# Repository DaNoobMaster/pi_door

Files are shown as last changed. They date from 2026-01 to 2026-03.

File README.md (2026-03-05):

#Pi_Door
This project is a smart door lock created using a raspberry pi zero 2w. This is the cheapest raspberry pi capable of running what i want this project needs.
The door is capable of Face ID, Palm vein recognition, fingerprint and has a 4x4 keypad entry as well. QR codes can be generated for one time use to open the door as well.
It uses high-end secure biometric components in order to keep it reliable and safe. There is a live camera feed as well that would be transmitted from the camera to the local raspberry pi server.

The aim of this project is to make entering my house quicker and more reliable. Due to the fact that its mostly digital, it is less susceptible to intruder attacks and can help catch intruders if an attack does occur. The live camera feed is also helpful in checking who is at your at door. I belive this project would use my skills to the most. Its mechanical and software aspect is perfect for me to improve my skills and learn how to work with such types of hardware.

The 4x3 keypad can be used to enter in a pincode.
The pincode can be set to be however long.
Pressing # enters the code while * resets it. If no user input is present for 10 seconds, the code entry cache resets. If the door unlocks using other means, the code entry cache resets.




### Complete Hardware Wiring

| Subsystem | Device Pin / Signal | Connected To | Raspberry Pi Pin | GPIO / Voltage | Notes |
|---|---|---|---|---|---|
| **AI Camera (Face / Palm)** | VCC | Pi 5V | Pin 4 | 5V | Camera power |
| AI Camera | GND | Pi GND | Pin 6 | GND | Common ground |
| AI Camera | UART_TX | Pi RX | Pin 10 | GPIO15 (RXD) | Camera → Pi |
| AI Camera | UART_RX | Pi TX | Pin 8 | GPIO14 (TXD) | Pi → Camera |
| **Fingerprint Sensor (via CP2102)** | VIN | CP2102 3V3 | — | 3.3V | Sensor power |
| Fingerprint | GND | CP2102 GND | — | GND | Common ground |
| Fingerprint | RX | CP2102 TXD | — | UART TX |
| Fingerprint | TX | CP2102 RXI | — | UART RX |
| Fingerprint | RST | CP2102 DTR | — | Reset |
| CP2102 | USB | Raspberry Pi | USB | — | USB-UART |
| **3×4 Keypad** | K1 (Row 1) | Pi GPIO | Pin 29 | GPIO5 | Output |
| Keypad | K2 (Row 2) | Pi GPIO | Pin 31 | GPIO6 | Output |
| Keypad | K3 (Row 3) | Pi GPIO | Pin 33 | GPIO13 | Output |
| Keypad | K4 (Row 4) | Pi GPIO | Pin 35 | GPIO19 | Output |
| Keypad | K5 (Col 1) | Pi GPIO | Pin 37 | GPIO26 | Input (PU) |
| Keypad | K6 (Col 2) | Pi GPIO | Pin 38 | GPIO20 | Input (PU) |
| Keypad | K7 (Col 3) | Pi GPIO | Pin 40 | GPIO21 | Input (PU) |
| Keypad | K8 | — | — | NC | Not connected |
| Keypad | K9 | — | — | NC | Not connected |
| Relay | Relay VCC | Pi 5V | Pin 4 | 5V | Coil power |
| Relay | Relay GND | Pi GND | Pin 6 | GND | Ground |
| **Transistor (BC107)** | Base | Pi GPIO (via resistor) | Pin 16 | GPIO23 | Drives relay |
| Transistor | Collector | 5V | — | 5V | From voltage convertor |
| Transistor | Emitter | Relay Coil | — | — | Reference |
| **Solenoid Lock** | + | External Supply | — | +7.5V | Lock power |
| Solenoid | − | Relay NO Contact | — | Switched | Controlled by relay |

### Authentication Accuracy & Error Rates

| Input Method | False Acceptance Rate (FAR) | False Rejection Rate (FRR) | Notes |
|---|---|---|---|
| Fingerprint (Capacitive) | ~0.001% – 0.01% | ~1% – 3% | High accuracy, may fail with wet or damaged fingers |
| Face Recognition (Offline AI) | ~0.1% – 1% | ~1% – 5% | Affected by lighting, pose, and occlusion |
| Palm Recognition (Offline AI) | ~0.01% – 0.1% | ~0.5% – 2% | Very stable, less affected by lighting |
| Keypad PIN (4-digit) | 0% (if secret) | User-dependent | Security depends on PIN secrecy and length |

BOM

| S.No | Component | Purpose | Estimated Cost (₹) |
|-----:|---|---|---:|
| 1 | Solenoid (Door Lock) | Physically locks/unlocks the door | 800 |
| 2 | Face ID & Palm Vein Sensor | Primary biometric authentication | 5636 |
| 3 | Fingerprint Sensor | Secondary authentication | 2,042.00 |
| 4 | Raspberry Pi Zero 2 W | Main controller & processing unit | 1,587.10 |
| 5 | 18650 Battery | Portable power source | 205.32 |
| 6 | Battery Charger Module | Charging the 18650 battery | 14.00 |
| 7 | Battery Holder | Secure battery mounting | 46.00 |
| 8 | UART Converter (CP2102) | Additional UART interface for fingerprint sensor | 300.00 |
| 9 | USB to Micro-USB Cable | Power & USB connection | 54.00 |
| 10 | Barrel Jack Connector | External power input | 23.00 |
| 11 | 4×3 Keypad | Manual PIN-based fallback access | 188.00 |
| 12 | BC107 Transistor | Solenoid driver / switching | 19.00 |
| 13 | 3D Printed Parts | Enclosure & mounting brackets | — |
| 14 | Acrylic Sheet | Structural housing panels | 75.00 |
| 15 | SRD-05VDC-SL-A Relay | Solenoid isolation & control | 79.00 |
| 16 | XL6009 | Boost converter | 50.00 |
| 17 | LM2596 | Buck converter | 44.00 |
| 17 | PCB | - | 222 |
| **—** | **Total Estimated Cost** |  | **11,744.32** |

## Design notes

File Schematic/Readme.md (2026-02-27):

This folder contains all PCB design related files

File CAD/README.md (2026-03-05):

This folder contains all the CAD files.

Some parts i could not find the CAD file for however i took their measurements from online and designed their chassis accordingly. Parts such as the fingerprint sensor and camera module do not have a cad available online, only measurements.

There is a routing Hole behind the fingerprint sensor, this is where the cables will pass through to reach the other side of the door
routing CAD

There are also routing tunnels present for the camera.
Modules on my PCB are not displayed either however PCB has been designed with their footprints so size should be exactly as required.

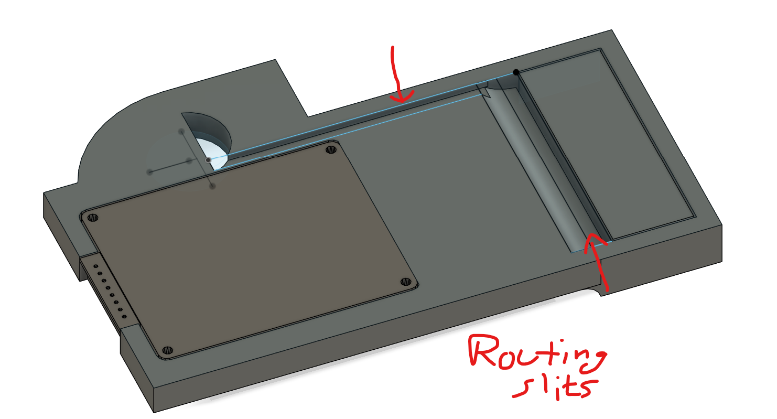
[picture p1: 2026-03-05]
CAD/routing CAD.png

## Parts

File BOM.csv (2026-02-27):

Item | Description | Quantity | Unit Price ( ? ) | Total Price ( ? ) | URL | Running Total After Discounts & Tax ( ? )
Solenoid ( to lock ) | Solenoid to push my door lock | 1 | 800.00 | 800.00 | https://robu.in/product/dc-12v-25n-10mm-push-pull-solenoid-electromagnet/ | 800.00
Face ID & Palm Vein sensor | high-performance biometric module offering Face Recognition, Palm Vein Detection, and QR Code Scanning | 1 | 5636.00 | 5636.00 | https://robu.in/product/offline-ai-binocular-3d-vision-recognition-sensor/ | 5636.00
Fingerprint Sensor | Highly secure optical fingerprint sensor | 1 | 2042.00 | 2042.00 | https://robu.in/product/waveshare-round-shaped-all-in-one-capacitive-fingerprint-sensor-d-cortex-processor-360-verification/ | 2042.00
Raspberry Pi Zero 2W | Used to interface between all components and create a web server to watch the video feed | 1 | 1581.00 | 1581.00 | https://quartzcomponents.com/products/raspberry-pi-zero-2-w?variant=44802854584554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 | 1940.00
18650 Battery | A high capacity Li-Ion battery @ 3000mAh & 3.7V | 2 | 62.00 | 124.00 | https://quartzcomponents.com/products/18650-li-ion-3-7v-3000mah-rechargeable-battery-winwaycopy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 | 205.32
TP4056 | Battery charging module for the Li-Ion Batteries | 1 | 15.00 | 15.00 | Buy TP4056 Battery Charger C Type Module with Protection – Robocraze | 15.00
Battery Holder | 2 18650 cells battery holder | 1 | 46.00 | 46.00 | https://robu.in/product/2-x-18650-black-battery-holder-with-dc-power-plug/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 | 46.00
UART Convertor | To use more than 1 UART device | 1 | 279.00 | 279.00 | https://www.amazon.in/CP2102-UART-Serial-Converter-Module/dp/B09HHHK2VR? | 300.00
USB to MicroUSB | To use on raspberry pi zero2 | 1 | 79.00 | 79.00 | https://robocraze.com/products/high-speed-micro-usb-otg-cable-33-cm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 | 54.00
Barrel Jack Connector | Barrel Jack Connectors to minimise error due to loose connection of flimsy wires | 1 | 23.00 | 23.00 | https://robu.in/product/male-female-2-15-5mm-dc-power-jack-adapter-connector-plug-cctv-camera/?gad_source=1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 | 23.00
4x3 keypad | To manually enter pincode | 1 | 157.00 | 157.00 | https://www.xcluma.com/keyboard-button-matrix-keyboard-3-4-3x4-keyboard-module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 | 186.00
BC107 transistor | To power relay using IO signal | 1 | 24.00 | 24.00 | https://robocraze.com/products/bc107-npn-general-purpose-transistor-metal-can-package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 | 19.00
3D print | The main housing for the build | 1
Acrylic Sheet | Transparent sheet for camera | 1 | 75.00 | 75.00 | https://robu.in/product/online-laser-cutting-service/ | 75.00
XL6009 | Voltage Booster | 1 | 49.00 | 49.00 | https://quartzcomponents.com/products/xl6009-dc-dc-boost-power-supply-module?variant=34741150417049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 | 58.00
SRD-05VDC-SL-A | Relay to control solenoid lock | 1 | 79.00 | 79.00 | https://robu.in/product/srd-05vdc-sl-a-ningbo-songle-relay-250vac-5v-15a-1-form-a-1a-spst-no-plugin15-6x19-2mm-power-relays-rohs/ | 79.00
LM2596 | Voltage Convertor step down | 1 | 44.00 | 44.00 | https://robu.in/product/lm2596s-dc-dc-buck-converter-power-supply/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 | 44.00
M3 Screw | For mounting Raspberry Pi | 2 | OWNED
M4 Screw | for camera mounting | 2 | OWNED
PCB | PCB to connect all parts together | 1 | 222.00 | 222 | https://jlcpcb.com/ | 222.00
M2 Screw | For keypad mounting | 4 | OWNED
3D Print | Chassis in which everything will lie | 1
Total Cost : |  |  |  |  |  | 11744.32

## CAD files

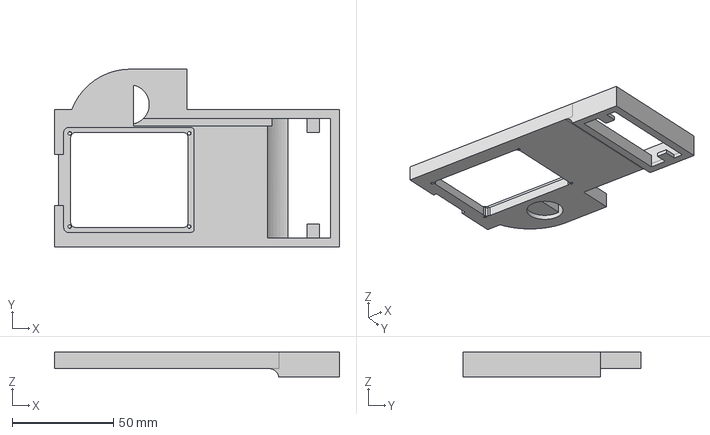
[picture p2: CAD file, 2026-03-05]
CAD/Body.step
140.7 x 87.8 x 12.1 mm

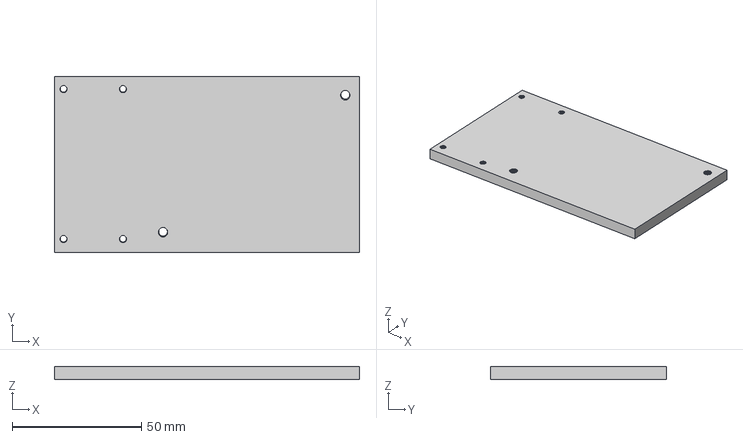
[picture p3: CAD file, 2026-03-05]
CAD/PCB mounting board.step
118.0 x 68.0 x 5.00 mm

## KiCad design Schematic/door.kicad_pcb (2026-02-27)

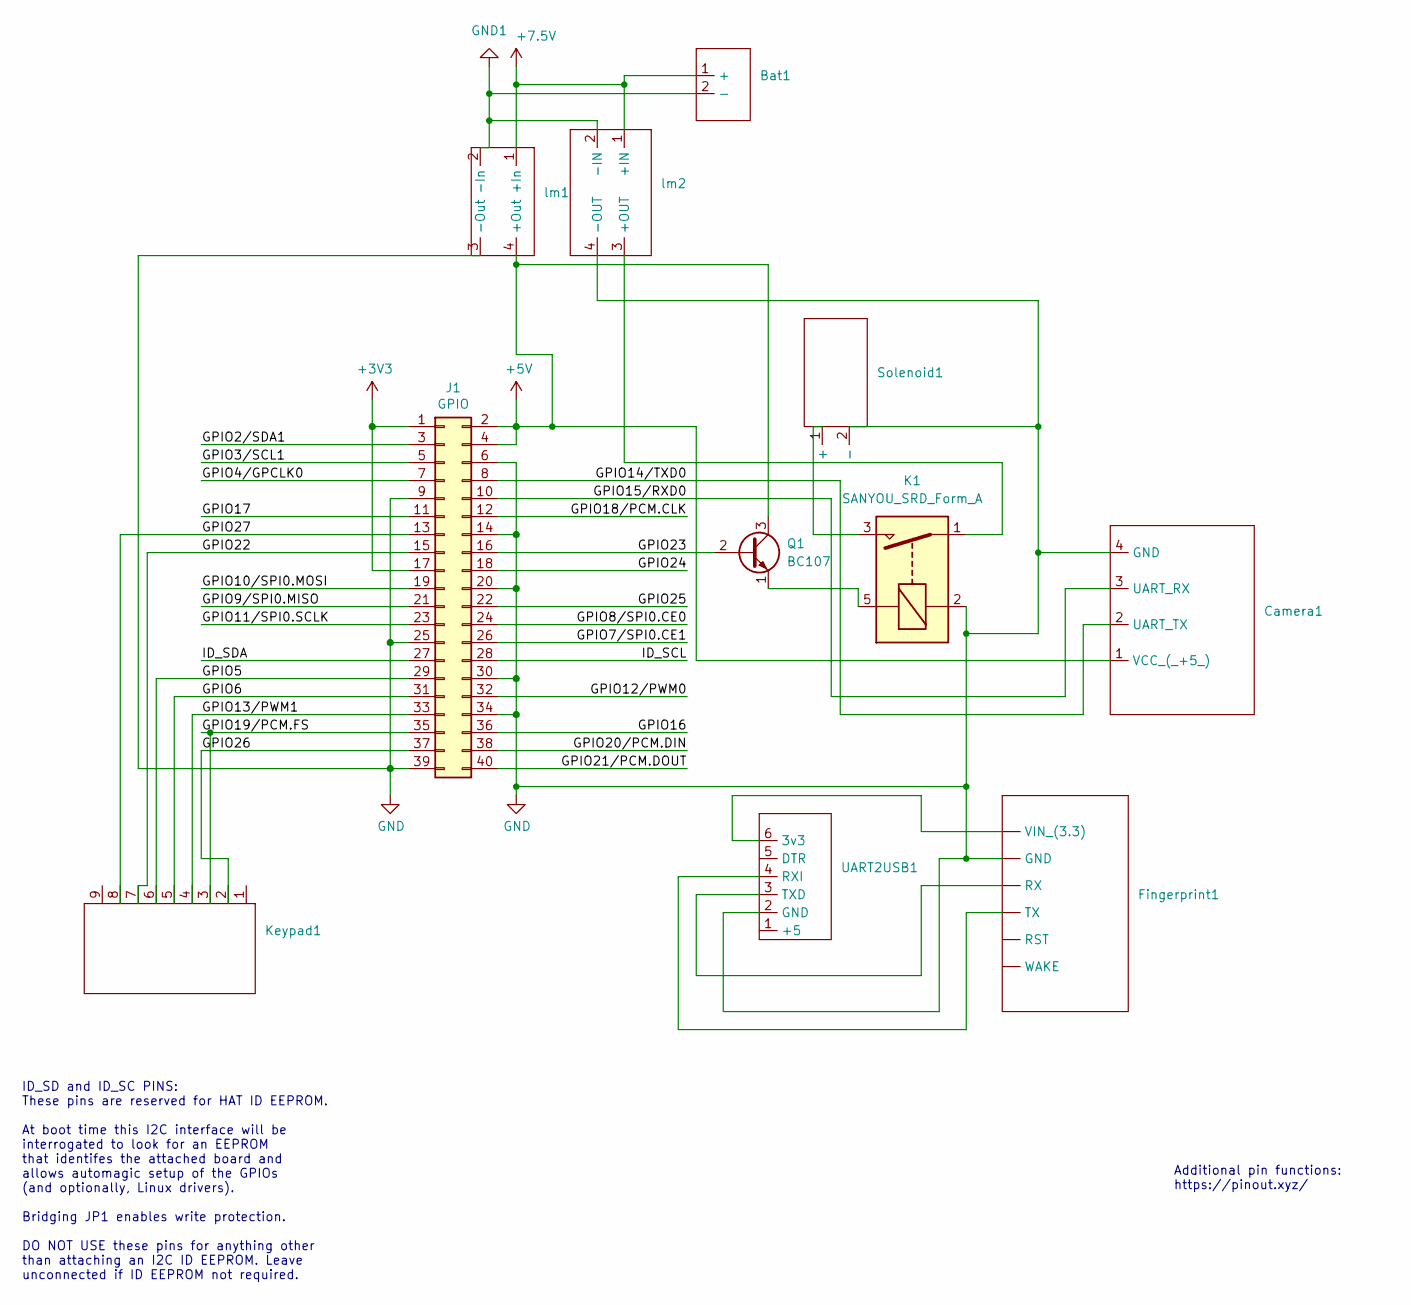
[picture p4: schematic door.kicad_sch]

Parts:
Bat1: Battery
Camera1: Camera
Fingerprint1: (no value)
J1: GPIO; PinSocket_2x20_P2.54mm_Vertical
K1: SANYOU_SRD_Form_A; Relay_SPST_SANYOU_SRD_Series_Form_A
Keypad1: Keypad
Q1: BC107; TO-18-3
Solenoid1: Solenoid
UART2USB1: CP2102
lm1: LM2596
lm2: XL6009_module

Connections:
+3V3: J1.1, J1.17
+5V: Camera1.1 (VCC_(_+5_)), J1.2, J1.4, Q1.3 (C), lm1.4 (+Out)
+7.5V: Bat1.1 (+), lm1.1 (+In), lm2.1 (+IN)
/GPIO2/SDA1: J1.3
/GPIO3/SCL1: J1.5
/GPIO4/GPCLK0: J1.7
/GPIO5: J1.29, Keypad1.6
/GPIO6: J1.31, Keypad1.5
/GPIO7/SPI0.CE1: J1.26
/GPIO8/SPI0.CE0: J1.24
/GPIO9/SPI0.MISO: J1.21
/GPIO10/SPI0.MOSI: J1.19
/GPIO11/SPI0.SCLK: J1.23
/GPIO12/PWM0: J1.32
/GPIO13/PWM1: J1.33, Keypad1.4
/GPIO14/TXD0: Camera1.2 (UART_TX), J1.8
/GPIO15/RXD0: Camera1.3 (UART_RX), J1.10
/GPIO16: J1.36
/GPIO17: J1.11
/GPIO18/PCM.CLK: J1.12
/GPIO19/PCM.FS: J1.35, Keypad1.3
/GPIO20/PCM.DIN: J1.38
/GPIO21/PCM.DOUT: J1.40
/GPIO22: J1.15, Keypad1.7
/GPIO23: J1.16, Q1.2 (B)
/GPIO24: J1.18
/GPIO25: J1.22
/GPIO26: J1.37, Keypad1.2
/GPIO27: J1.13, Keypad1.8
/ID_SCL: J1.28
/ID_SDA: J1.27
GND: Camera1.4 (GND), Fingerprint1., J1.6, J1.9, J1.14, J1.20, J1.25, J1.30, J1.34, J1.39, K1.2, Solenoid1.2 (-), UART2USB1.2 (GND), lm1.3 (-Out), lm2.4 (-OUT)
GND1: Bat1.2 (-), lm1.2 (-In), lm2.2 (-IN)
unnamed: Fingerprint1., UART2USB1.3 (TXD)
unnamed: Fingerprint1., UART2USB1.4 (RXI)
unnamed: Fingerprint1., UART2USB1.6 (3v3)
unnamed: K1.5, Q1.1 (E)
unnamed: K1.3, Solenoid1.1 (+)
unnamed: K1.1, lm2.3 (+OUT)

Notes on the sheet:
ID_SD and ID_SC PINS: These pins are reserved for HAT ID EEPROM. At boot time this I2C interface will be interrogated to look for an EEPROM that identifes the attached board and allows automagic setup of the GPIOs (and optionally, Linux drivers). Bridging JP1 enables write protection. DO NOT USE th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
Additional pin functions: https://pinout.xyz/

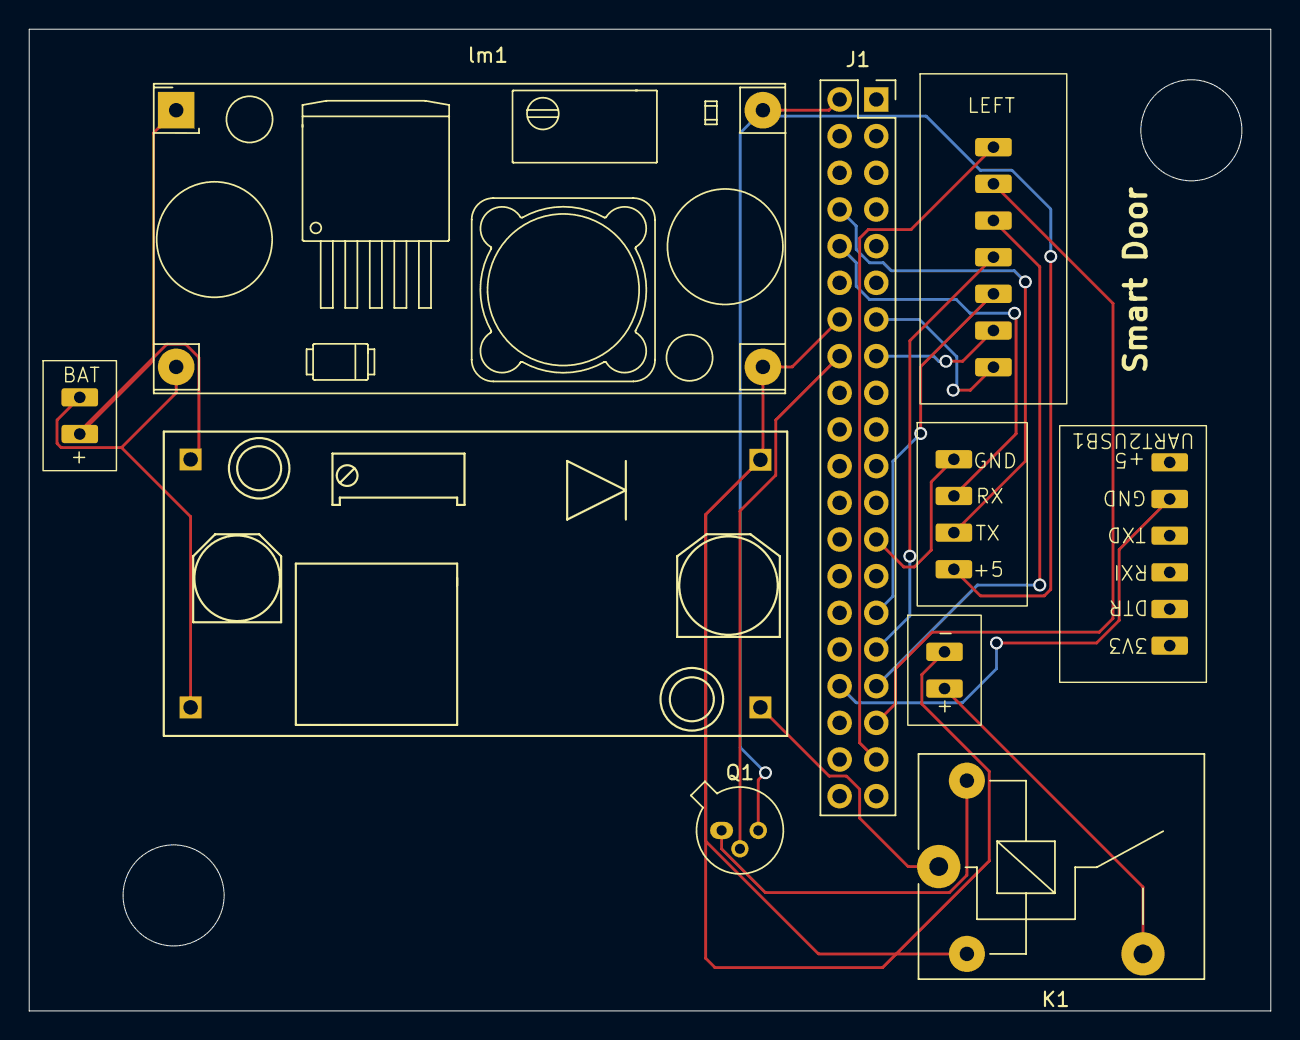
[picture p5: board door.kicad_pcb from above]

Board: 2 copper layers, 86.0 x 68.0 mm, 10 parts (0 on the bottom side), 18 nets.

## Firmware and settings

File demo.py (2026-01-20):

#!/usr/bin/env python3
# -*- coding: utf-8 -*-

import time
import serial
import RPi.GPIO as GPIO
from DFRobot_AI10 import DFRobot_AI10_UART

# =========================================================
# ======================== CONFIG =========================
# =========================================================

PIN_CODE = "1234"          # CHANGE THIS
PIN_TIMEOUT = 10           # seconds
UNLOCK_TIME = 5            # seconds door stays unlocked

# =========================================================
# ======================== GPIO ===========================
# =========================================================

GPIO.setmode(GPIO.BCM)
GPIO.setwarnings(False)

# Keypad pins (FROM YOUR SCHEMATIC)
KEYPAD_ROWS = [5, 6, 13, 19]
KEYPAD_COLS = [26, 20, 21]

KEYPAD_MAP = [
    ['1','2','3'],
    ['4','5','6'],
    ['7','8','9'],
    ['*','0','#']
]

for r in KEYPAD_ROWS:
    GPIO.setup(r, GPIO.OUT)
    GPIO.output(r, GPIO.HIGH)

for c in KEYPAD_COLS:
    GPIO.setup(c, GPIO.IN, pull_up_down=GPIO.PUD_UP)

# =========================================================
# ====================== KEYPAD ===========================
# =========================================================

def get_key():
    for r_idx, r in enumerate(KEYPAD_ROWS):
        GPIO.output(r, GPIO.LOW)
        for c_idx, c in enumerate(KEYPAD_COLS):
            if GPIO.input(c) == GPIO.LOW:
                time.sleep(0.2)  # debounce
                GPIO.output(r, GPIO.HIGH)
                return KEYPAD_MAP[r_idx][c_idx]
        GPIO.output(r, GPIO.HIGH)
    return None


def check_pin():
    entered = ""
    last_key_time = time.time()

    print("Enter PIN (* = clear, # = enter):")

    while True:
        if time.time() - last_key_time > PIN_TIMEOUT:
            if entered:
                print("\nPIN timeout → reset")
            return False

        key = get_key()
        if key:
            last_key_time = time.time()

            if key == '*':
                entered = ""
                print("\nPIN cleared")

            elif key == '#':
                print("\nPIN submitted")
                return entered == PIN_CODE

            else:
                entered += key
                print("*", end="", flush=True)

        time.sleep(0.1)

# =========================================================
# =============== FINGERPRINT (WAVESHARE) =================
# =========================================================

ACK_SUCCESS = 0x00
ACK_NO_USER = 0x05

CMD_HEAD = 0xF5
CMD_TAIL = 0xF5

CMD_ADD_1    = 0x01
CMD_ADD_3    = 0x03
CMD_MATCH    = 0x0C
CMD_USER_CNT = 0x09

USER_MAX_CNT = 1000

fp_ser = serial.Serial("/dev/ttyUSB0", 19200, timeout=1)
fp_rx_buf = []


def fp_txrx(cmd, rx_len, timeout):
    global fp_rx_buf
    checksum = 0
    packet = [CMD_HEAD]

    for b in cmd:
        packet.append(b)
        checksum ^= b

    packet.append(checksum)
    packet.append(CMD_TAIL)

    fp_ser.flushInput()
    fp_ser.write(bytes(packet))

    fp_rx_buf = []
    start = time.time()

    while time.time() - start < timeout and len(fp_rx_buf) < rx_len:
        if fp_ser.in_waiting:
            fp_rx_buf += list(fp_ser.read(fp_ser.in_waiting))

    if len(fp_rx_buf) != rx_len:
        return False

    if fp_rx_buf[0] != CMD_HEAD or fp_rx_buf[-1] != CMD_TAIL:
        return False

    return True


def fp_get_user_count():
    cmd = [CMD_USER_CNT, 0, 0, 0, 0]
    if fp_txrx(cmd, 8, 0.2) and fp_rx_buf[4] == ACK_SUCCESS:
        return fp_rx_buf[3]
    return -1


def register_fingerprint():
    print("Place finger to REGISTER...")
    time.sleep(1)

    count = fp_get_user_count()
    if count < 0 or count >= USER_MAX_CNT:
        return False

    cmd = [CMD_ADD_1, 0, count + 1, 3, 0]
    if fp_txrx(cmd, 8, 6) and fp_rx_buf[4] == ACK_SUCCESS:
        cmd[0] = CMD_ADD_3
        return fp_txrx(cmd, 8, 6) and fp_rx_buf[4] == ACK_SUCCESS

    return False


def check_fingerprint():
    print("Checking FINGERPRINT...")
    time.sleep(1)

    cmd = [CMD_MATCH, 0, 0, 0, 0]
    if not fp_txrx(cmd, 8, 5):
        return False

    return fp_rx_buf[4] != ACK_NO_USER

# =========================================================
# ================= AI10 CAMERA (FACE/PALM) ================
# =========================================================

ai10 = DFRobot_AI10_UART(115200)
ai10.begin()


def register_biometric(user_name="User", admin=False, timeout=10):
    print("Present FACE or PALM to REGISTER...")
    time.sleep(1)

    result = ai10.enroll_user(
        admin=ai10.ADMIN if admin else ai10.NORMAL,
        user_name=user_name,
        timeout=timeout
    )
    return result.result == ai10.Success


def check_biometric(timeout=5):
    print("Checking FACE or PALM...")
    data = ai10.get_recognition_result(timeout)
    return data.result == ai10.Success

# =========================================================
# ===================== AUTH LOGIC ========================
# =========================================================

def authenticate():
    # Biometric camera
    if check_biometric():
        print("Biometric success → PIN reset")
        return True

    # Fingerprint
    if check_fingerprint():
        print("Fingerprint success → PIN reset")
        return True

    # Keypad PIN
    if check_pin():
        print("PIN success")
        return True

    return False

# =========================================================
# ====================== MAIN LOOP =========================
# =========================================================

if __name__ == "__main__":
    try:
        print("🔐 Smart Door Lock Ready")

        while True:
            if authenticate():
                print("🔓 DOOR UNLOCKED")
                time.sleep(UNLOCK_TIME)
            else:
                print("❌ ACCESS DENIED")

            time.sleep(1)

    except KeyboardInterrupt:
        GPIO.cleanup()
        fp_ser.close()
        print("\nSystem stopped")

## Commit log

2026-01-19 Create Prototype Script.py
2026-01-20 Schematic folder
